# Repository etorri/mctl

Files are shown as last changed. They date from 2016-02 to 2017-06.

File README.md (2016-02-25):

# Objective

The purpose of this pile of rubbish is to build a controller between
Raspberry Pi UART (or SPI) and Pololu 708 (Dual VNH2SP30 Motor Driver
Carrier MD03A) with two DC gear motors (FIT0277).

The controller is based on msp430G2553 (20-pin) because I have several of them.
Besides that, it has nice peripherals to implement

- wall clock with timer A0 to measure time intervals (encoders)
- sufficiently fast two channel PWM (10-20KHz) with timers A1
- UART,SPI or I2C clock
- interrupts from the rotary encoders of the motors.
- just enough IO ports

The code is designed for this particular application. It may have
useful components and "Notes to Self" comments that somebody finds
useful.

# Control?

The Pi tells the controller to

- Initialize
- Break
- Prepare to run
- Run with given PWM values
- Error recovery
- Sleep

The controller reports back to Pi

- state of the controller
- position and speed (and current) of the two motors
- errors reported by the driver chip

# Pins wasted

The following pins of the msp430G2553 are misused for the purpose
(see the eagle files)

Left side, top to down

| Pin# | Port | Function | Description      |
|------+------+----------+------------------|
|    1 | DVCC | +3.3v    | Electrons exit   |
|    2 | P1.0 | IO       | out: L ENA       |
|    3 | P1.1 | UART RX  | data from Pi     |
|    4 | P1.2 | UART TX  | data to Pi       |
|    5 | P1.3 | IO       | in : L DIAG      |
|    6 | P1.4 | IO       | in : L Encoder B |
|    7 | P1.5 | IO       | in : L Encoder A |
|    8 | P2.0 | IO       | out: L INB       |
|    9 | P2.1 | TA1.1    | out: L PWM       |
|   10 | P2.2 | IO       | out: L INA       |

Right Side, top to down

| Pin# | Port | Function | Description       |
|------+------+----------+-------------------|
|   20 | DVSS | +0v      | Electrons enter   |
|   19 | P2.6 | IO       | out: R ENA        |
|   18 | P2.7 | IO       | in : R DIAG       |
|   17 | x    | TEST     | Programmer        |
|   16 | x    | RESET    | Programmer        |
|   15 | P1.7 | IO       | in :  R Encoder B |
|   14 | P1.6 | IO       | in :  R Encoder A |
|   13 | P2.5 | IO       | out: R INB        |
|   12 | P2.4 | TA1.2    | out: R PWM        |
|   11 | P2.3 | IO       | out: R INA        |

The motor driver also provides two Current Sense (CS) analog outputs
that tell how many amps go through a motor.

# CPU settings

Low power operation (at which the msp430 is also good at) is not
within the scope. It runs full speed 16MHz from the DCO oscillator.

# Motor control signals to the driver

The controller will handle the confusion that left motor will turn
Clockwise (CW) and right CounterClockWise (CCW) when going forward. 
The Power settings received from the Pi are signed integers bounded
by the timer A1 TA1CCR0 count (PWM frequency).
Negative number means going backwards and positive forwards.

Three states of INA and INB motor driver pins are used 

| State | L INA | L INB | R INA | R INB |
|---|---|---|---|---|
| Power(x) >= 0 | 1 | 0 | 0 | 1 |
| Power(x) < 0  | 0 | 1 | 1 | 0 |
| Braking | 0 | 0 | 0 | 0 |

Braking state means shorting both motors to ground. With the 51:1 gears
this shouldn't really be necessary.

The PWM has 10KHz frequency and motor driver documentation says max 20KHz.
DCO clock 16MHZ with

The driver operates at 5v and high level signal is 3.27v which is
uncomfortably close to the 3.3v of msp430 so level converters are needed.

The INA, INB pins in MSP need to be in the same port to be able to change
them simultaneously. Otherwise the motor might be in braking mode for
a short period. Documentation mentions 

Example:

~~~~
#define LINA BIT4 
#define LINB BIT3
P2OUT = (P2OUT&~LINB)|LINA; // Left motor forward in one op
P2OUT = (P2OUT&~LINA)|LINB; // Left motor backward
P2OUT &= ~(LINA|LINB);      // Left Brake
~~~~

# Encoder signals from the motors

*Speculation based on the vague docs, need to be verified with the hardware*

Hall effect quadrature encoder will give 13 interrupts per 
one motor rotation on the A input. The gearbox is 51:1 which makes it
663 interrupts per one rotation of the wheel.

At 16MHz it seems that by initial measurements
this MSP430 chip can handle 160K interrupts per second 
or 80K interrupts/s per wheel with highly unoptimized C code ISRs.
So the ISR is bounded with wheel speeds of 120r/s. The motor+gear documentation
mentions ~3 r/s for top speed which makes me believe this should not be a problem.

The accuracy looks pretty good when measured with the 2MHz wall clock
timer implemented with T0. Connecting the PWM output to encoder A input
gives variation of one step (0.5 microseconds).

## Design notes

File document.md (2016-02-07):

# Two channel 10KHz PWM with msp430G2553

## Timer A0 pwm left motor

CCR1 = output
- port p1.6
- P1DIR[6]=1, P1SEL[6]=1

## Timer A1 pwm right motor

CCR1
- port p2.1
-

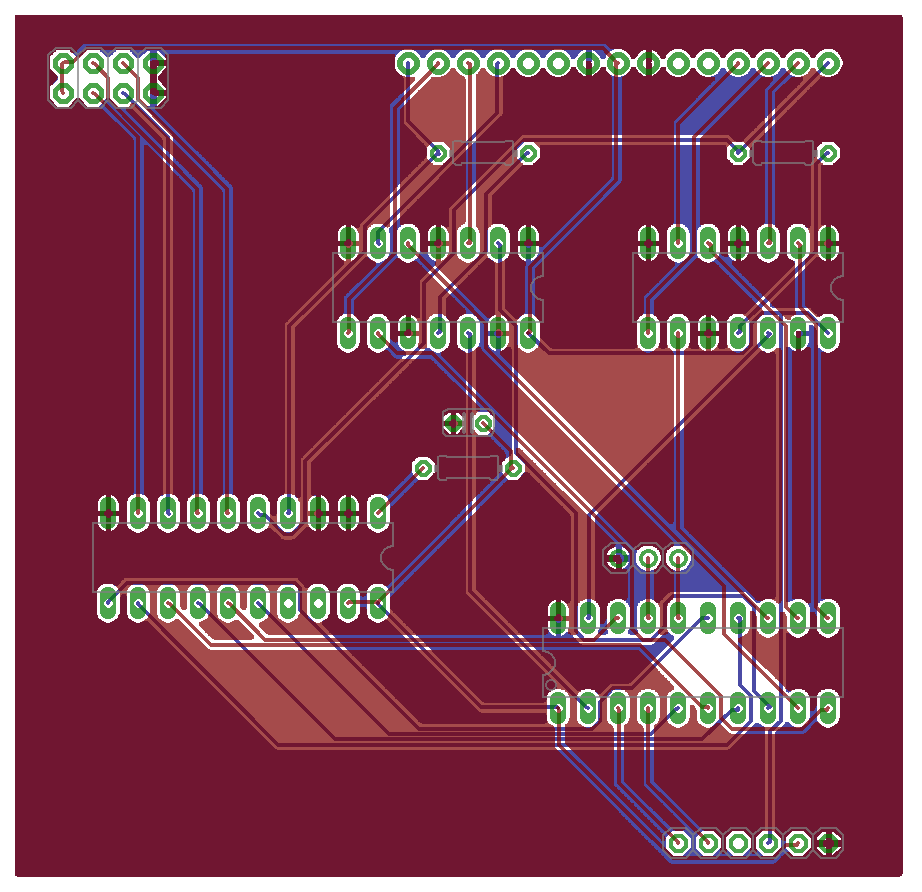
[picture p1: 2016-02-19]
docs/eagle/mctl5.png

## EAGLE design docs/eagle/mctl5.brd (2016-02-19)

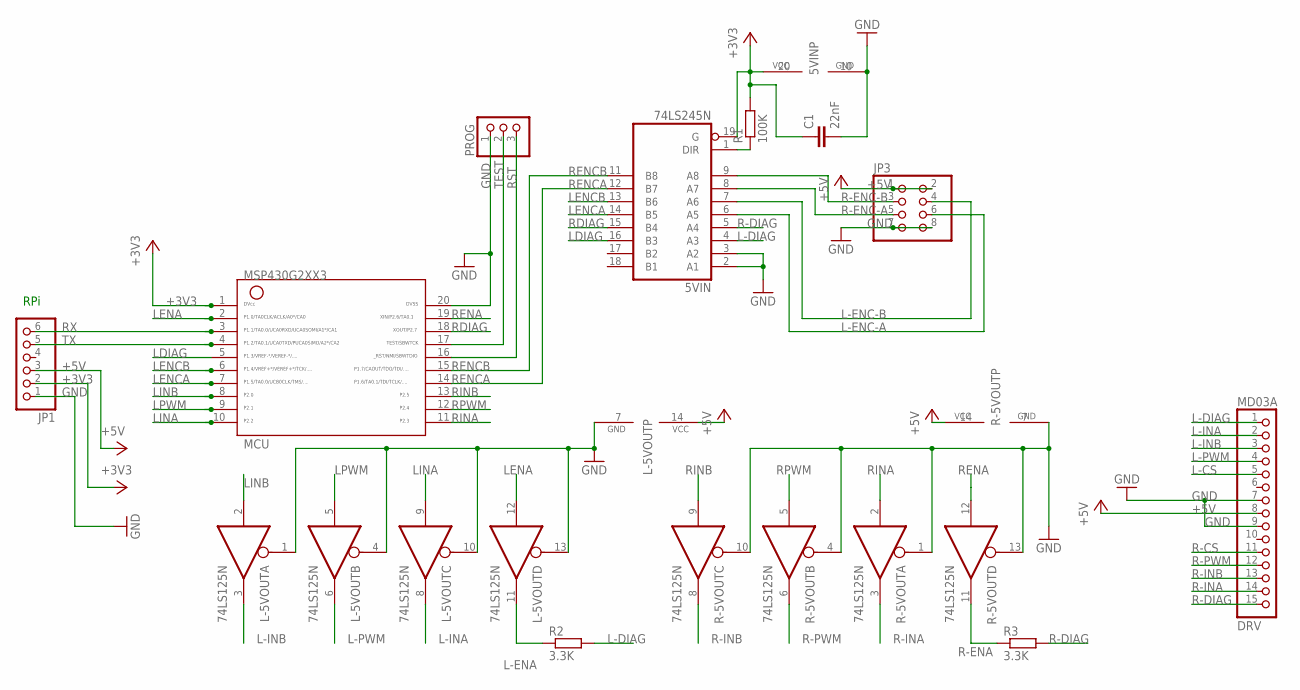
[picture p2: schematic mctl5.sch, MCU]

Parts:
5VIN: 74LS245N; DIL20
C1: 22nF; C025-024X044
JP1: PINHD-1X6; 1X06
JP3: PINHD-2X4; 2X04
L-5VOUT: 74LS125N; DIL14
MCU: G2XX3---N20; N20
MD03A: DRV; 1X15-CB
PROG: PINHD-1X3; 1X03
R1: 100K; 0204/7
R2, R3: 3.3K; 0204/7
R-5VOUT: 74LS125N; DIL14

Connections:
+3V3: 5VIN.19 (G), 5VIN.20 (VCC), C1.1, JP1.2, MCU.1, R1.2
+5V: JP1.3, JP3.1, JP3.2, L-5VOUT.14 (VCC), MD03A.8, R-5VOUT.14 (VCC)
GND: 5VIN.2 (A1), 5VIN.3 (A2), 5VIN.10 (GND), C1.2, JP1.1, JP3.7, JP3.8, L-5VOUT.1 (OE), L-5VOUT.4 (OE), L-5VOUT.7 (GND), L-5VOUT.10 (OE), L-5VOUT.13 (OE), MCU.20, MD03A.7, MD03A.9, PROG.1, R-5VOUT.1 (OE), R-5VOUT.4 (OE), R-5VOUT.7 (GND), R-5VOUT.10 (OE), R-5VOUT.13 (OE)
L-CS: MD03A.5
L-DIAG: 5VIN.4 (A3), MD03A.1, R2.2
L-ENA: L-5VOUT.11 (O), R2.1
L-ENC-A: 5VIN.6 (A5), JP3.6
L-ENC-B: 5VIN.7 (A6), JP3.4
L-INA: L-5VOUT.8 (O), MD03A.2
L-INB: L-5VOUT.3 (O), MD03A.3
L-PWM: L-5VOUT.6 (O), MD03A.4
LDIAG: 5VIN.16 (B3), MCU.5
LENA: L-5VOUT.12 (I), MCU.2
LENCA: 5VIN.14 (B5), MCU.7
LENCB: 5VIN.13 (B6), MCU.6
LINA: L-5VOUT.9 (I), MCU.10
LINB: L-5VOUT.2 (I), MCU.8
LPWM: L-5VOUT.5 (I), MCU.9
unnamed: 5VIN.1 (DIR), R1.1
R-CS: MD03A.11
R-DIAG: 5VIN.5 (A4), MD03A.15, R3.2
R-ENA: R3.1, R-5VOUT.11 (O)
R-ENC-A: 5VIN.8 (A7), JP3.5
R-ENC-B: 5VIN.9 (A8), JP3.3
R-INA: MD03A.14, R-5VOUT.3 (O)
R-INB: MD03A.13, R-5VOUT.8 (O)
R-PWM: MD03A.12, R-5VOUT.6 (O)
RDIAG: 5VIN.15 (B4), MCU.18
RENA: MCU.19, R-5VOUT.12 (I)
RENCA: 5VIN.12 (B7), MCU.14
RENCB: 5VIN.11 (B8), MCU.15
RINA: MCU.11, R-5VOUT.2 (I)
RINB: MCU.13, R-5VOUT.9 (I)
RPWM: MCU.12, R-5VOUT.5 (I)
RST: MCU.16, PROG.3
RX: JP1.6, MCU.3
TEST: MCU.17, PROG.2
TX: JP1.5, MCU.4

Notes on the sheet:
RPi

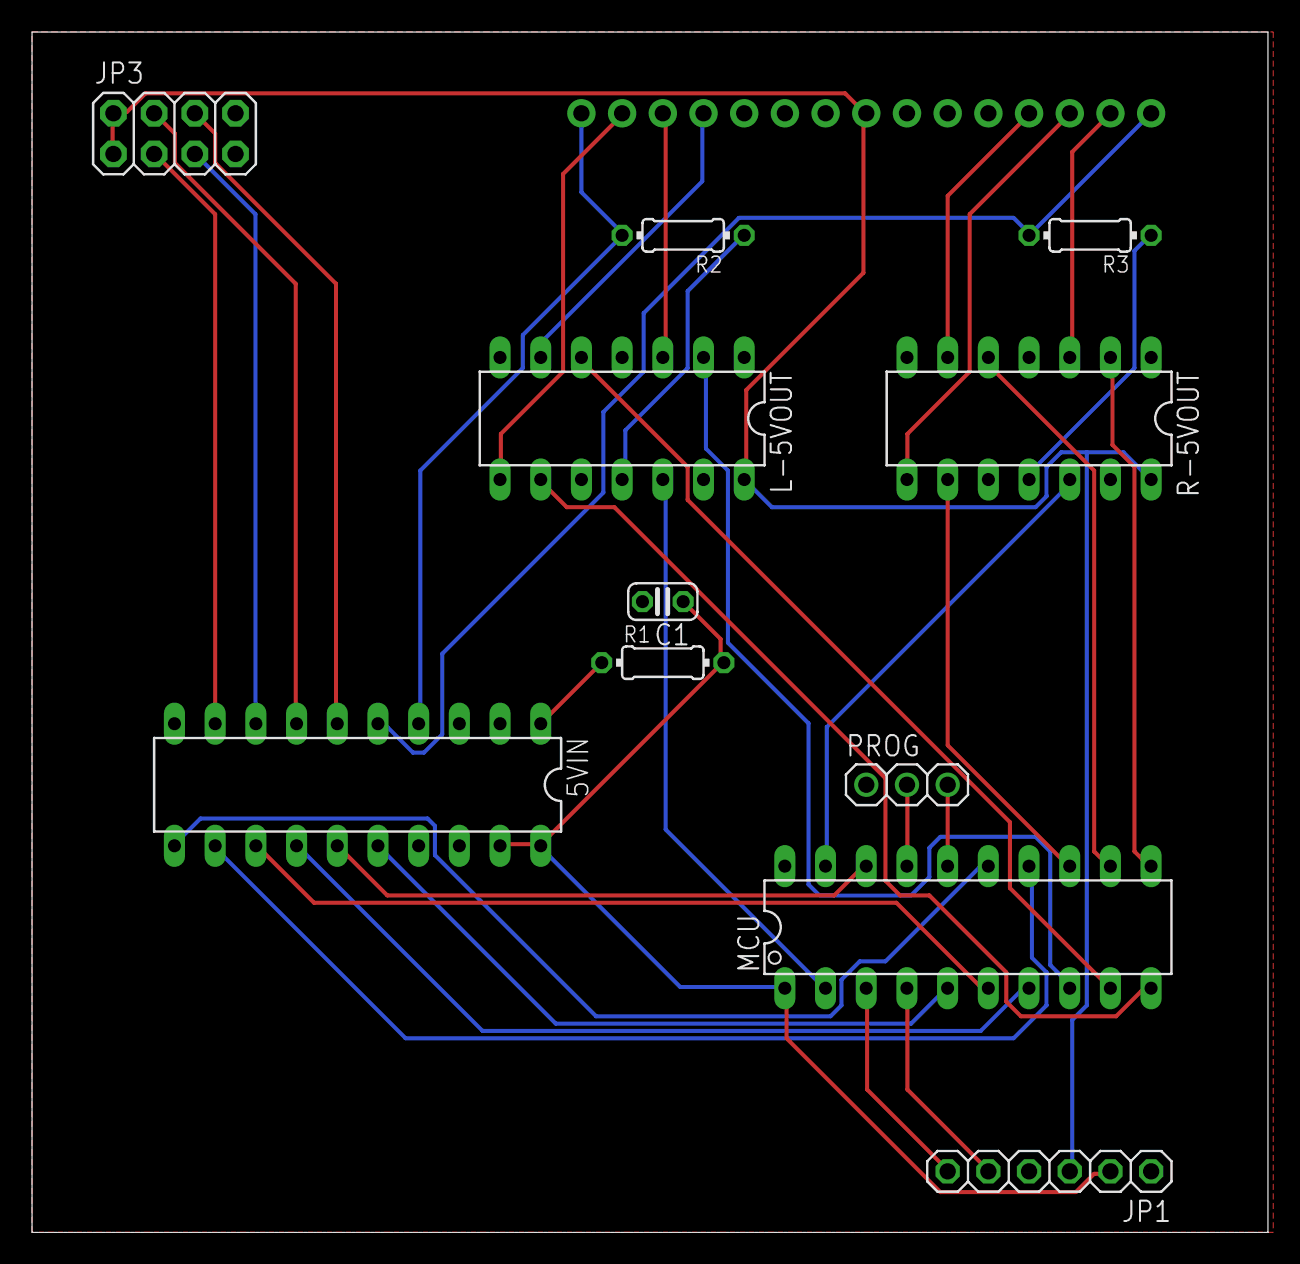
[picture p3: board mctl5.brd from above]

Board: 2 copper layers, 77.1 x 74.9 mm, 12 parts (0 on the bottom side), 36 nets.

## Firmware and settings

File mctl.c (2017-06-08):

#include "clock.h"
#include "pwm.h"
#include "motor.h"
#include "uart.h"
#include "interrupts.h"
#include "protocols.h"
#include <msp430g2553.h>

#define PAUS __delay_cycles(1600000)
#define FOREVER while(1)

// Watchdog controls
#define WD_HOLD  WDTCTL = (WDTPW|WDTHOLD)
// Clear, select VLO clock (4KHz..20Khz, nominal 12KHz), divide by 8192
#define WD_CLEAR WDTCTL = (WDTPW|WDTCNTCL)
// WDT_ARST_1000
// (WDTPW|WDTCNTCL|WDTSSEL_2|WDTIS_2)


int main(void) {
  WD_HOLD;
  // configure the CPU clock (MCLK)
  // to run from SMCLK: DCO @ 16MHz and SMCLK = DCO
  // If no DCO calibration => stop here by loop
  if(CALBC1_16MHZ==0xff)
    while(1)
      _NOP();

  // ------- without interrupts
  _BIC_SR(GIE);
  //DCOCTL = 0;
  BCSCTL1= CALBC1_16MHZ;
  DCOCTL = CALDCO_16MHZ;
  //BCSCTL3= LFXT1S_2;     // VLO source
  PAUS;
  // initialize modules
  clock_init();
  pwm_init();
  motor_init();
  uart_init();
  protocols_init();

  // ------- interrupts enabled 
  _BIS_SR(GIE);
  WD_CLEAR;
  
  FOREVER {
    WD_CLEAR;
    // deal with possible input bytes from uart
    input_scanner();
    WD_CLEAR;
    // execute the possible input command
    motor_step();
    WD_CLEAR;
    // send status report
    reporter();
  }
}

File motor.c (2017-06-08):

#include <msp430g2553.h>
#include <inttypes.h>
#include <stdlib.h>
#include "motor.h"
#include "pwm.h"
#include "clock.h"
#include "protocols.h"

// Motor control ports
// left INA port 2.0
#define LINA BIT0
// left INB port 2.2
#define LINB BIT2
// left DIAG port 2.6
#define LDIAG BIT6
// right INA port 2.3
#define RINA BIT3
// right INB port 2.5
#define RINB BIT5
// right DIAG port 2.7
#define RDIAG BIT7

// Encoder pins at port 1
#define LENCA BIT5
#define LENCB BIT4
#define RENCA BIT6
#define RENCB BIT7

// communication to/from the motor
motor_in m_in;
motor_out m_out;

volatile uint8_t mmsg=0;

// internal motor control variables
static   int16_t left_power;  
static   int16_t right_power;
// timeout timer to detect broken communication with pi
static  uint32_t power_timer;

// forward definitions
static inline void motor_set_power(void);
static inline void motor_ready(void);



// ----------------------------------------------------------------------
// --- initialize encoder inputs
//
void encoder_init(void){
  // clear position counters
  m_out.l_pos = m_out.r_pos = 0;
  // configure encoder pins
  P1SEL &= ~(LENCA|LENCB|RENCA|RENCB); // as gpio
  P1DIR &= ~(LENCA|LENCB|RENCA|RENCB); // as inputs
  P1IE  |= (RENCA|LENCA);              // A pins as interrupts
  P1IES &=  ~(RENCA|LENCA);            // rising edge
  // configure DIAG pins
  P2SEL &= ~(LDIAG|RDIAG);             // as gpio
  P2DIR &= ~(LDIAG|RDIAG);             // as input
  P2IE  |= (LDIAG|RDIAG);              // enable interrupt
  P2IES |= (LDIAG|RDIAG);              // falling edge
  
}

// ----------------------------------------------------------------------
// --- prepare motor driver for the READY state (stopped, breaking)
//
static inline void
motor_ready(void){
  // set pwm to 0
  left_power=right_power=0;
  motor_set_power();
  // motor in breaking state
  P2OUT &= ~(LINA|LINB|RINA|RINB);
}


// ----------------------------------------------------------------------
// --- Initialize the motor subsystem - called by mctl.c
// 
void
motor_init(void) {
  // configure INA/INB pins
  P2SEL  &= ~(LINA|LINB|RINA|RINB); // as gpio
  P2DIR  |= (LINA|LINB|RINA|RINB);  // as outputs
  // P2SEL2 &= ~(LINA|LINB|RINA|RINB); 
  P2IE   &= ~(LINA|LINB|RINA|RINB); 
  // initialize variables
  m_out.state=MSTATE_READY;
  m_in.msg=0;
  // do what is needed to enter the READY state
  motor_ready();
  encoder_init();
  // start with READY state so reporting interval is longer
  report_interval=READY_REPORT_INTERVAL;
}



// ----------------------------------------------------------------------
// --- Set the power for left motor
//
static inline void
motor_set_left(int power) {
  int8_t sgn;
  sgn= (power>=0);
  power=abs(power);
  if(sgn) {
    // power is positive => CW
    P2OUT = (P2OUT|LINA)&(~LINB);
  }else{
    // power is negative => CCW
    P2OUT = (P2OUT|LINB)&(~LINA);
  }
  pwm_l_set(power);
}


// ----------------------------------------------------------------------
// --- Set the power for right motor
//
static inline void
motor_set_right(int power) {
  int8_t sgn;
  sgn= (power>=0);
  power=abs(power);
  // set direction based on the sign of the power setting
  if(sgn) {
    P2OUT = (P2OUT|RINA)&(~RINB);
  }else{
    P2OUT = (P2OUT|RINB)&(~RINA);
  }
  // call helper to set the PWM
  pwm_r_set(power);
}


// ----------------------------------------------------------------------
// --- Set the power for both motors
//


static inline void
motor_set_power(void){
  motor_set_right(right_power);
  motor_set_left(left_power);
}



// ----------------------------------------------------------------------
// --- state machine to handle messages (in mmsg variable)
//
// the mmsg is set by protocols.c:input_scanner and any kind of failure
// detection mechanism. There is a risk for timing conflicts


void motor_step(void) {
  switch(m_out.state){
  case MSTATE_READY:
    // inputs
    if(mmsg&MMSG_FAIL){
      motor_ready();
      m_out.state=MSTATE_FAIL;
      report_interval=READY_REPORT_INTERVAL;
    } else if(mmsg&MMSG_POWER) {
      left_power=m_in.l_pwr;
      right_power=m_in.r_pwr;
      motor_set_power();
      set_timer(&power_timer);
      m_out.state=MSTATE_RUN;
      report_interval=RUN_REPORT_INTERVAL;
    }
    // clear inputs
    mmsg=0;
    break;
	  
  case MSTATE_RUN:
    // if Pi is not talking frequently enough (dead?) stop everything
    // and do not keep driving towards the cliff
    if(interval_elapsed(&power_timer,MAX_POWER_SETTING_INTERVAL)){
      mmsg=MMSG_FAIL;
    }
    // inputs
    if(mmsg&MMSG_FAIL) {
      motor_ready();
      report_interval=READY_REPORT_INTERVAL;
      m_out.state=MSTATE_FAIL;
      mmsg=0;
    } else if(mmsg&MMSG_POWER) {
      set_timer(&power_timer);
      left_power=m_in.l_pwr;
      right_power=m_in.r_pwr;
      motor_set_left(left_power);
      motor_set_right(right_power);
      m_out.state=MSTATE_RUN;
    } else if(mmsg&MMSG_STOP) {
      motor_ready();
      m_out.state=MSTATE_READY;
      report_interval=READY_REPORT_INTERVAL;
    }
    // clear inputs
    mmsg=0;
    break;

  case MSTATE_FAIL:
    // inputs
    if(mmsg&MMSG_CLEAR){
      m_out.state=MSTATE_READY;
      report_interval=READY_REPORT_INTERVAL;
    }
    // clear inputs and keep steady 
    mmsg=0;
    motor_ready();
    break;
  }
}


// ----------------------------------------------------------------------
// --- Interrupt Service Routines for rotary encoders and driver failures
//


// Encoders at port 1
void __attribute__((interrupt (PORT1_VECTOR))) p1isr() {
  // Left encoder interrupt
  if(P1IFG & LENCA) {
    // If L-ENC-B also up then going forward
    if(P1IN & LENCB){
      m_out.l_pos++;
    }else{
      m_out.l_pos--;
    }
    // Clear LENCA interrupt
    P1IFG &= ~LENCA;
  }
  // Right encoder interrupt
  if(P1IFG & RENCA) {
    // In right motor R-ENC-A and R-ENC-B means backwards
    if(P1IN & RENCB){
      m_out.r_pos--;
    }else{
      m_out.r_pos++;
    }
    // Clear RENCA interrupt
    P1IFG &= ~RENCA;
  }
}

// Motor driver diagnostic inputs at port 2
void __attribute__((interrupt (PORT2_VECTOR))) p2isr() {
  // RDIAG went down = Right motor fail
  if(P2IFG & RDIAG){
    P2IFG &= ~RDIAG;
    mmsg|= MMSG_FAIL;
  }
  // L-DIAG (2.6) went down = Left motor fail
  if(P2IFG & LDIAG){
    P2IFG &= ~LDIAG;
    mmsg|= MMSG_FAIL;
  }
}

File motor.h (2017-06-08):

#ifndef MOTOR_H
#define MOTOR_H

//  --------------- Motor states --------------
#define MSTATE_READY    1 // idle
#define MSTATE_RUN      2 // running
#define MSTATE_FAIL     4 // motor driver (or test) failure state

// ---------------- messages to motor ----------
#define MMSG_POWER      1 // pwm settings command
#define MMSG_STOP       2 // stop
#define MMSG_FAIL       4 // signal motor failure
#define MMSG_CLEAR      8 // clear motor failure
// ---------------- messages to Pi ----------
// Status report to the Pi (motor state, direction, speed, position)
#define MMSG_REPORT     49

// go to FAIL state from RUN state if not receiving power settings
// with this interval = 1/10s ( < 16cm at full speed )
#define MAX_POWER_SETTING_INTERVAL 2000000


// Input message to the motor
struct mi {
  volatile int16_t l_pwr;
  volatile int16_t r_pwr;
  volatile uint8_t msg; // message to the state machine 
}  __attribute__((__packed__));

typedef struct mi motor_in;


// output message from the motor
// note: MSP architecture requires that 16-bit values
//       can only be read from even addresses.
//       If there are odd number of uint8 before uint16
//       this would cause there be a hole and sizeof()
//       would return unexpect results.
struct mo {
  volatile int32_t l_pos;  
  volatile int32_t r_pos;  
  volatile uint32_t framing_errors;
  volatile uint8_t msg;    
  volatile uint8_t state;  
  volatile uint8_t error;
} __attribute__((__packed__));

typedef struct mo motor_out;

extern motor_in m_in;
extern motor_out m_out;

extern volatile uint8_t mmsg;

extern void motor_init(void);
extern void motor_step(void);


#endif

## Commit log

2016-02-10 New modules: Encoder interrupt handlers, wall clock Changed: pwm now with timer 1 only, documentation with changed pin organization
2016-02-14 Add: Motor control (direction, power), buffered uart, chip documents
2016-02-19 First test version of motor driver controller
    Additional feature: ENAble signal for both motors which pulls the DIAG/ENA line to +5V with 3.3K resistor.
    This moves the motor driver to low-power state when not driving. It also keeps the motor driver disabled
    at start until the controller decides to start it.
    [mctl5.brd, mctl5.sch]
2016-03-09 Moving to separate uart input, output handling
2016-03-31 Packet length problems: MSP aliasing and last-but-one error in counter
    [mctl.c, motor.c, motor.h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]
